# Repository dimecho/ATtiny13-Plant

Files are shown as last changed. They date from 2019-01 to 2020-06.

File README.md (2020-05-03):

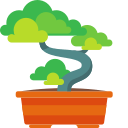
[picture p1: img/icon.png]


# ATtiny13 Plant

Monitor soil moisture and water plant. Portable and high efficiency with lithium-ion batteries.

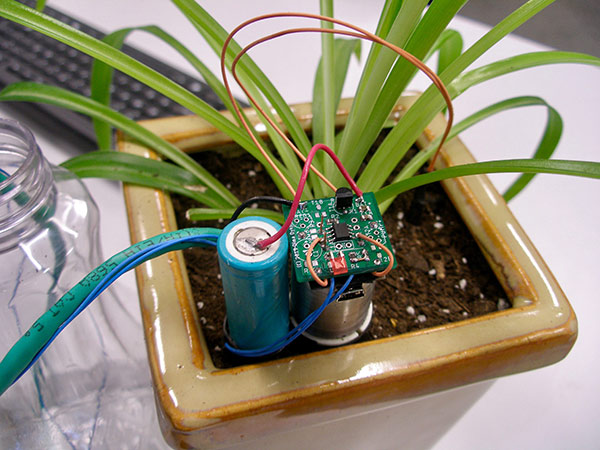
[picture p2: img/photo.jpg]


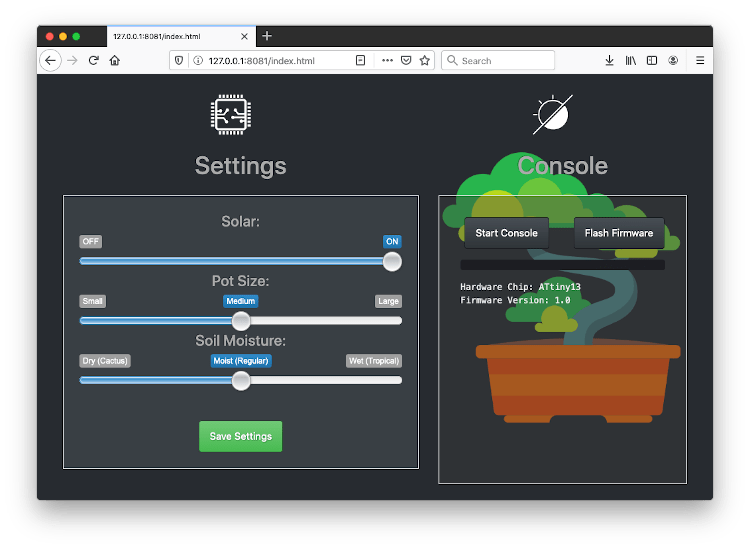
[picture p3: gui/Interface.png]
GUI


## Download

MacOS [MacOS](../../releases/download/1.0/ATtiny13-Plant.dmg)

Windows [Windows](../../releases/download/1.0/ATtiny13-Plant.zip)

Linux [Linux](../../releases/download/1.0/ATtiny13-Plant.tgz)

Firmware [Firmware](../../releases/download/1.0/ATtiny13-Plant-Firmware.zip)

## BOM (Bill of Materials)

| Part  | Value | Package | Function |
| ----- |:---:| ---:|---:|
| IC1 | ATTINY13A  | SOP-8 or DIP-8 | CPU |
| C1 | 100nF | 0805 or 0603 (104)  | CPU |
| T1A/B | 2N4401 NPN | TO-92 or SOT-23 | Pump |
| R1 | 100R | 0805 or 0603 (101)  | Pump |
| R2 | 10k | 0805 or 0603 (103)  | Pump |
| R6 | 10k | 0805 or 0603 (103)  | Sensor |
| LED1  | Red | 0805 or DIP-2 | LED |
| R7 | 1k | 0805 or 0603 (102)  | LED |
| - | 3.7-4.2V | Lithium 18650 | Battery  |
| - | TP4056 | Lithium Charger | Charger  |

## PCB

Designed with [EagleCAD](https://www.autodesk.com/products/eagle/free-download)

## Diagram

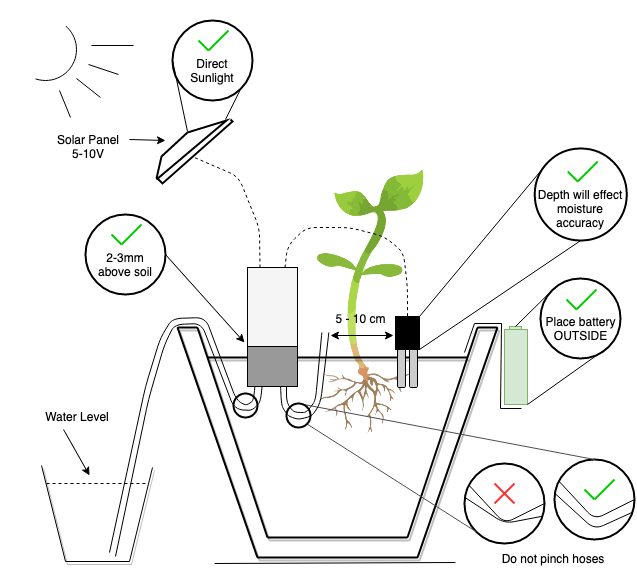
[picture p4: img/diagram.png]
Diagram


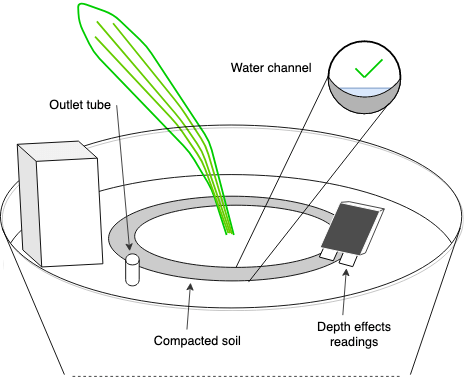
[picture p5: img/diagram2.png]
Operational


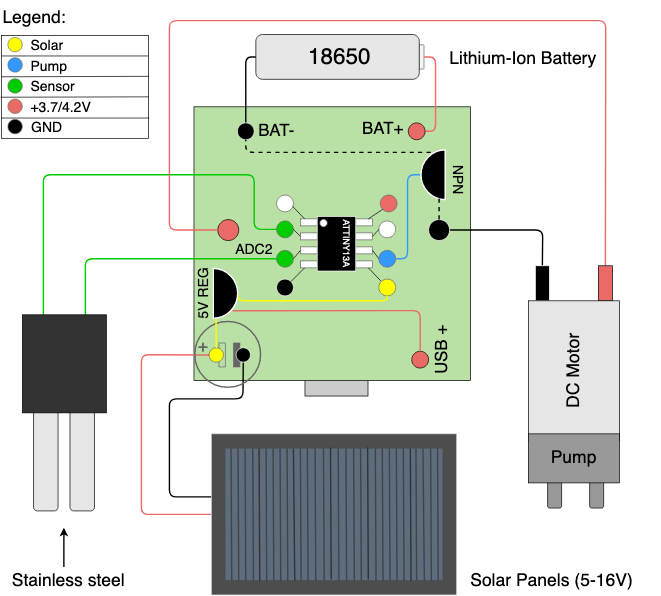
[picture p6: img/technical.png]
Technical


## Compile

Install "avr-gcc" and run "make".

> [MacOS](https://ww1.microchip.com/downloads/en/DeviceDoc/avr8-gnu-toolchain-osx-3.6.2.503-darwin.any.x86_64.tar.gz)
>
> [Windows](https://ww1.microchip.com/downloads/en/DeviceDoc/avr8-gnu-toolchain-3.6.2.1759-win32.any.x86.zip)

```
avr-gcc -std=gnu99 -Wall -Os -mmcu=attiny13a main.c -o main.o
avr-objcopy -O binary main.o main.bin
avr-objcopy -O ihex main.o main.hex
```

## Flash

```
avrdude -p t13 -c usbtiny -Uhfuse:w:0xFB:m -Ulfuse:w:0x6A:m -U flash:w:main.hex:i
```

There are 3 options to flash ATtiny13 chip.

1. [USBtiny](usbtiny) (built-in)
2. [USBasp](usbasp)
3. [Raspberry Pi](usbpi)

## Licenses

> ATtiny13 Plant
>
> 
>
> USBasp / USBtiny
>
> GNU (https://www.gnu.org/licenses/)

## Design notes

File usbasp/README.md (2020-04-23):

USBASP KEY
==========

http://fabiobaltieri.com/2011/09/02/usb-key-avr-programmer/

This project is an AVR ISP programmer with USB interface in a compact usb
key PCB. The project is based on the original USBasp version of Thomas Fischl,
which can be found on:

http://www.fischl.de/usbasp/

Contents
--------

    COPYING     text version of the GPL
    README      this file
    binaries/   pre-built firmware images in hex format
    firmware/   source directory for firmware files
    hardware/   source directory for the hardware design files

Firmware
--------

Building requires an avr-gcc toolchain, in the firmware/ directory, to build
run:

    make main.hex

Flashing the firmware on the device requires avrdude and a compatible hardware
programmer. Default configuration is stored at the beginning of the Makefile.
To program with the default configuration, run:

    make flash

Fuses can be configured running:

    make fuses

Hardware
--------

All hardware files (schematic, layout and libraries) are in CadSoft Eagle
format.

```
avrdude -p t13 -c usbasp -Uhfuse:w:0xFB:m -Ulfuse:w:0x6A:m -U flash:w:main.hex:i
```

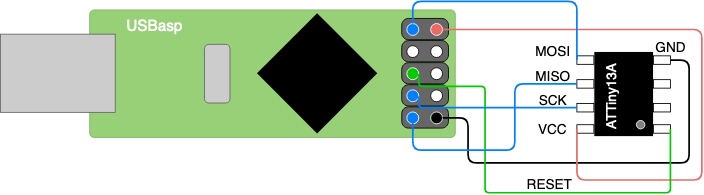
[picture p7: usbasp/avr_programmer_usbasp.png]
USBASP


License
-------

This program is free software: you can redistribute it and/or modify
it under the terms of the GNU General Public License as published by
the Free Software Foundation, either version 2 of the License, or
(at your option) any later version.

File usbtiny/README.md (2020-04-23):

http://www.simpleavr.com/avr/vusbtiny

Description
-------

From http://www.xs4all.nl/~dicks/avr/usbtiny/

USBtiny is a software implementation of the USB low-speed protocol for the Atmel ATtiny microcontrollers. Of course, it will also work on the ATmega series. The software is written for an AVR clocked at 12 MHz. At this frequency, each bit on the USB bus takes 8 clock cycles, and with a lot of trickery, it is possible to decode and encode the USB waveforms by software. The USB driver needs approximately 1250 to 1350 bytes of flash space (excluding the optional identification strings), depending on the configuration and compiler version, and 46 bytes RAM (excluding stack space). The C interface consists of 3 to 5 functions, depending on the configuration.

vUSB
-------

From http://www.obdev.at/products/vusb/

V-USB is a software-only implementation of a low-speed USB device for Atmel's AVR microcontrollers, making it possible to build USB hardware with almost any AVR microcontroller, not requiring any additional chip.

Features
-------

* Programming logic from usbtiny isp, mature avr-dude support
* Small foot-print
* Minimal components
* Powers target device

Note that the IO lines to the target MCUS are not protected. you can add 1k-2k resistors to SCK and MOSI and protect against possible wrong connections

References
-------

based on the works found at

v-usb from framework http://www.obdev.at/vusb/
usbtiny isp http://www.xs4all.nl/~dicks/avr/usbtiny/

Parts List
-------

* 1x attiny45/85
* 1x 100nf capacitor (104)
* 2x 3.6v zener diodes (1n747,BZX79)
* 2x 68ohm resistor
* 1x 1.5k (1.7k) resistor

* (optional) 1k/2k resistors for io lines protection

Tools Required
-------
* A working AVR programmer (yes, it's a catch22, we need one to make one)
* Working AVR programming environment

Application Notes
-------

* vusbtiny works with avrdude and is viewed by avrdude as a usbtiny programmer
* vusbtiny always power target chip via USB
* Jumper J2 connects programmer to target chip
* When connected and NOT in programming
* Target chip w/ target RESET line high
* Other target pins (MISO, MOSI, CLK) in hi-Z state
* During programming
* Turns target RESET line LOW
* MISO becomes input
* MOSI, CLK becomes output

Schematic
-------

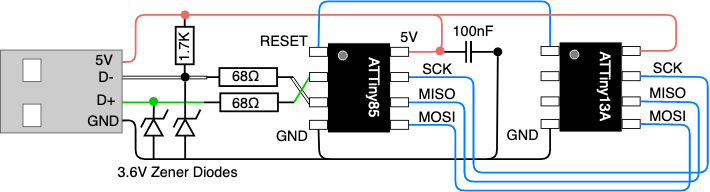
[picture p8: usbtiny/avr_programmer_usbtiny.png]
USBTINY


Building and Flashing
-------

* change into /firmware working directory
```
make
```
* attach your favorite ISP programmer
* modify makefile and change your avrdude parameters if needed. the stock one assumes USBTiny programmer. i.e. AVRDUDE_PROGRAMMERID=usbtiny
```
make install
```
After flashing firmware, we need to properly set the fuse, we are using pin 1 reset as IO in this project

* PLL clock used as required by v-usb layer for usb timing (16.5Mhz)
* reset pin disabled as we need to use it as IO
```
avrdude -c usbtiny -p t85 -V -U lfuse:w:0xe1:m -U hfuse:w:0x5d:m -U efuse:w:0xff:m
```

This setting disables further programming via 5V SPI as we need the RESET pin (pin1) for IO. you will need access to a HVSP programmer to recover the fuse.

Troubleshooting
-------

* Cannot flash the firmware? check your original programmer, might need to adjust timing via -B flag in avrdude. try to read chip 1st, may be a bad fuse, may be your chip need an external clock signal. you may need to fix your chip back to default 1st.
    check connections
* If use different io pins, check code and connections
* You may substitute zener diodes with 500mw, 400mw types
* You may try reduce R3 value to 1.2K or less
* You are more likely to encounter avrdude timing problems, try -B flag of avrdude, have a shorter USB cable all helps

License
-------

GPL2

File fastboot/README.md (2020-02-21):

### Bootloader

Bootloader is usefull for updating the firmware over UART without desoldering the chip. It also frees up RESET pin as IO (see Caution note).

Compile
```
cd ./bootloader
make
```
One-Time Flash
```
avrdude -p t13 -c linuxgpio -Uhfuse:w:0xEE:m -Ulfuse:w:0x6A:m -e -U flash:w:bootload.hex:i
```
Update (MacOS)
```
./fastboot/osx/bootloader -d /dev/cu.usbserial -b 9600 -p main.hex
```
Update (Windows)
```
./fastboot/win/FBOOT.EXE -C2 -B9600 -Pmain.hex
```

**Caution:** RESET Pin1 (PB5) if fuses set HFuse 0xFE (or 0xEE), bootloader can only be flashed once. Future flashing requires "High-Voltage programmer" to clear the fuse.

## License

GNU (https://www.gnu.org/licenses/)

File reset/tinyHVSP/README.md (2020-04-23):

http://www.simpleavr.com/avr/hvsp-fuse-resetter

Description
-------

Revert RESET fuse to factory default fuse settings.

Features
-------

* Reads device signature and hi-low fuses for hi-voltage serial programmable attinys
* Reset hi-low fuses to factory default on target devices
* Layout to drop-on attiny13, attiny25/45/85 8 pin devices targets
* Attiny24/44/84 targets needs additional breadboard and jumper wires
* Standalone operations, fuses values show on 7 segment display
* Cannot reset fuse for attiny2313 and atmega devices as they requires hi-voltage parallel programming

Parts List
-------

* attiny2313
* 4x7 segment LED display
* 1k resistor x 2
* 2n2222 NPN transistor or equivalent
* 78L05
* +12V battery source

Schematic
-------

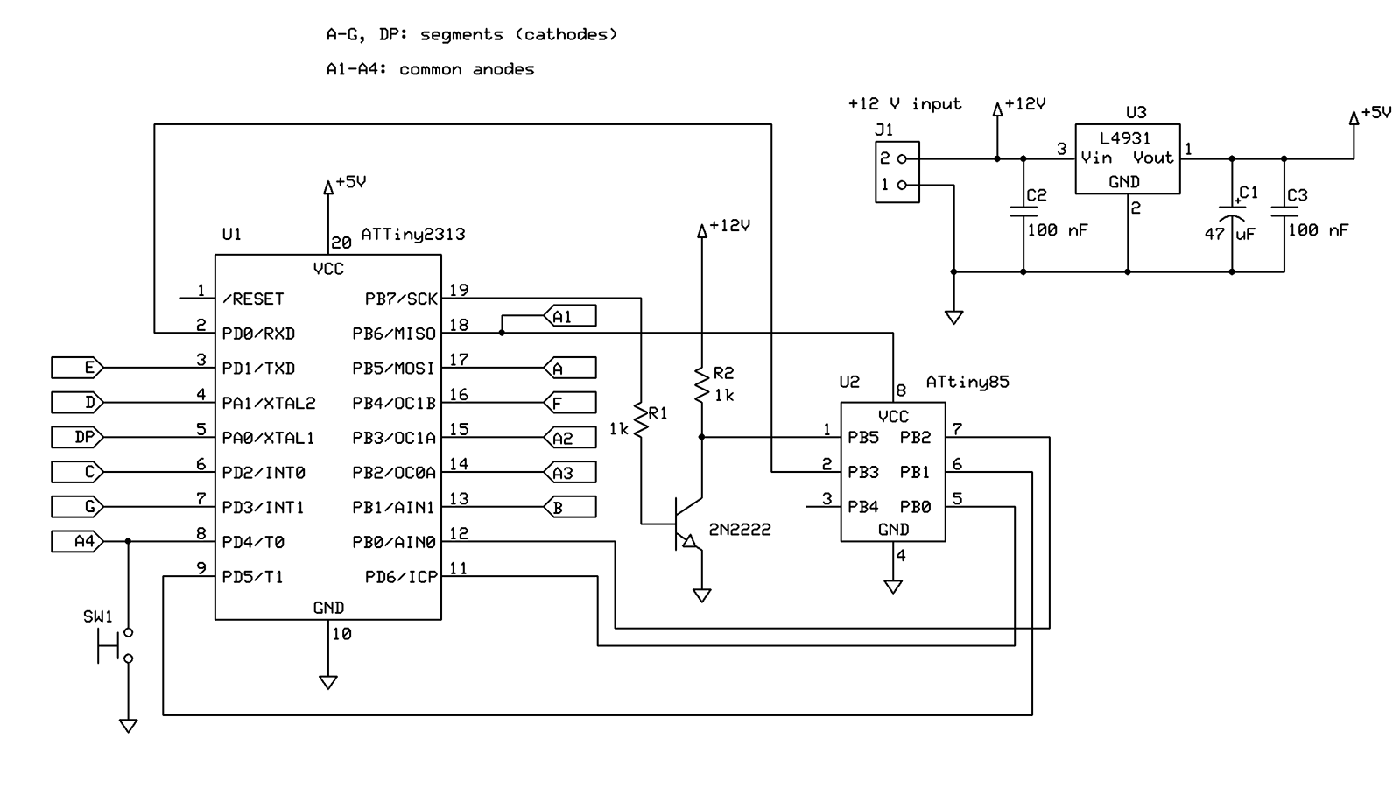
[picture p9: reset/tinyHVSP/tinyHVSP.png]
Schematic


Project FUSE Setting
-------

```
avrdude -c usbtiny -p t2313 -V -U lfuse:w:0xe4:m -U hfuse:w:0xdf:m -U efuse:w:0xff:m
```

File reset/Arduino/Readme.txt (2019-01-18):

Wire-up ATTiny chip into Arduino that needs its fuses fixed (see schematics for details) and load ATTinyFuseReset.ino sketch. In the Arduino IDE open Serial Monitor and select 19200 baud as the serial rate. Then send a character to the Arduino using the Serial Monitor's "send" button to trigger the fuse reset cycle. The code will print out the device signature and before and after values of the fuses.

You should now have a functional ATTiny!

Source: https://sites.google.com/site/wayneholder/attiny-fuse-reset

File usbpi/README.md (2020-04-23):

## Flash ATtiny13 with Raspberry Pi (linuxgpio)
```
avrdude -p t13 -c linuxgpio -Uhfuse:w:0xFB:m -Ulfuse:w:0x6A:m -U flash:w:main.hex:i
```

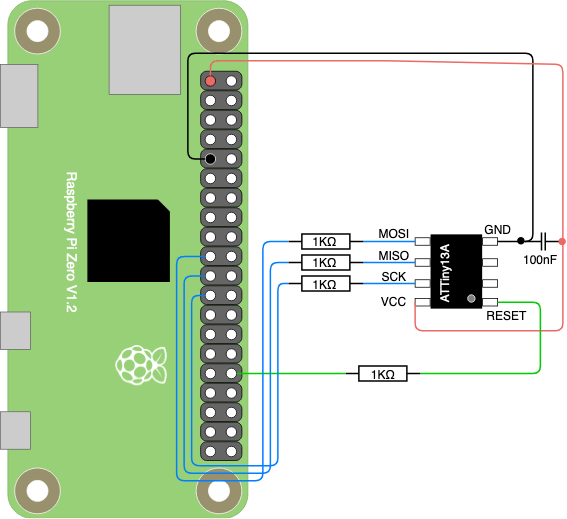
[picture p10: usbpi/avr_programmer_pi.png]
PI


Install AVRDude.
```
sudo apt-get install avrdude
```
Open AVRDude configuration file for editing.
```
sudo nano /etc/avrdude.conf
```
In Nano, use ctrl-w to search for linuxgpio. This is the section that controls the GPIO pins used for programming. The section needs to be uncommented. Set the MOSI, MISO and SCK entries to the GPIO pins on the Pi.
```
programmer
  id    = "linuxgpio";
  desc  = "Use the Linux sysfs interface to bitbang GPIO lines";
  type  = "linuxgpio";
  reset = 12;
  sck   = 11;
  mosi  = 10;
  miso  = 9;
```

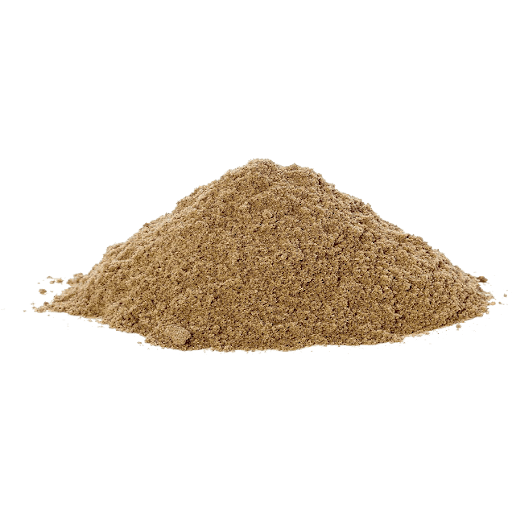
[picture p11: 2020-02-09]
gui/Web/img/sand.png

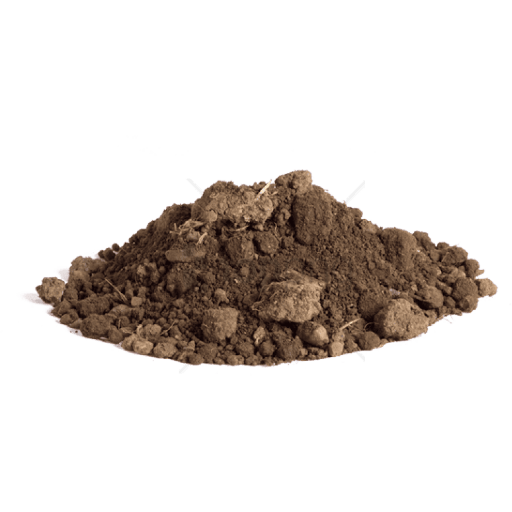
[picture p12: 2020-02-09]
gui/Web/img/dirt.png

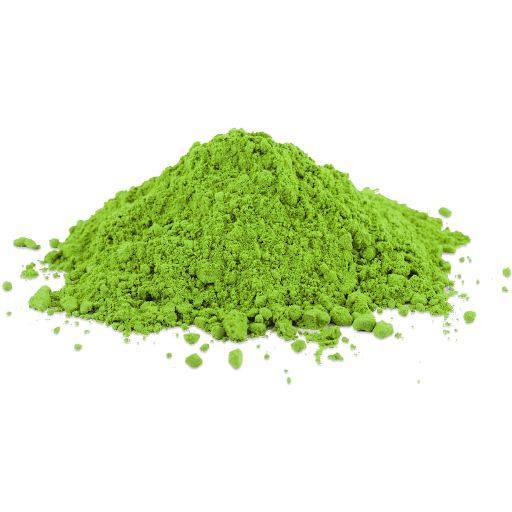
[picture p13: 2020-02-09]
gui/Web/img/moss.png

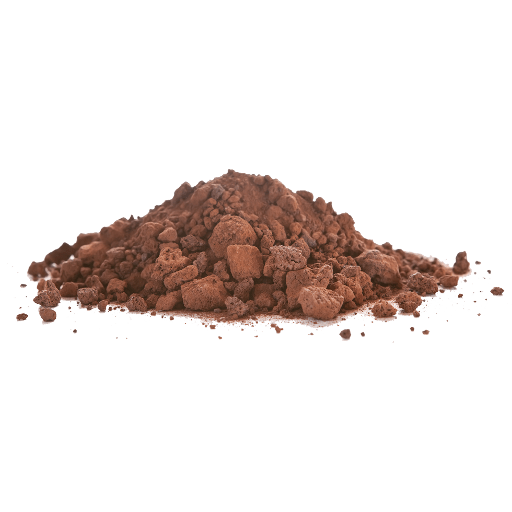
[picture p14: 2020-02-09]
gui/Web/img/clay.png

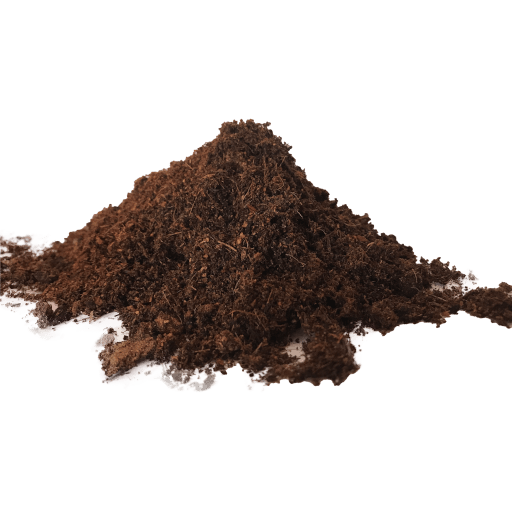
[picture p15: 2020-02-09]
gui/Web/img/loam.png

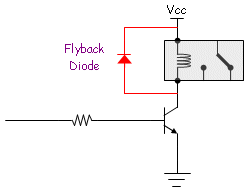
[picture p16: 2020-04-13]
img/flyback_diode.png

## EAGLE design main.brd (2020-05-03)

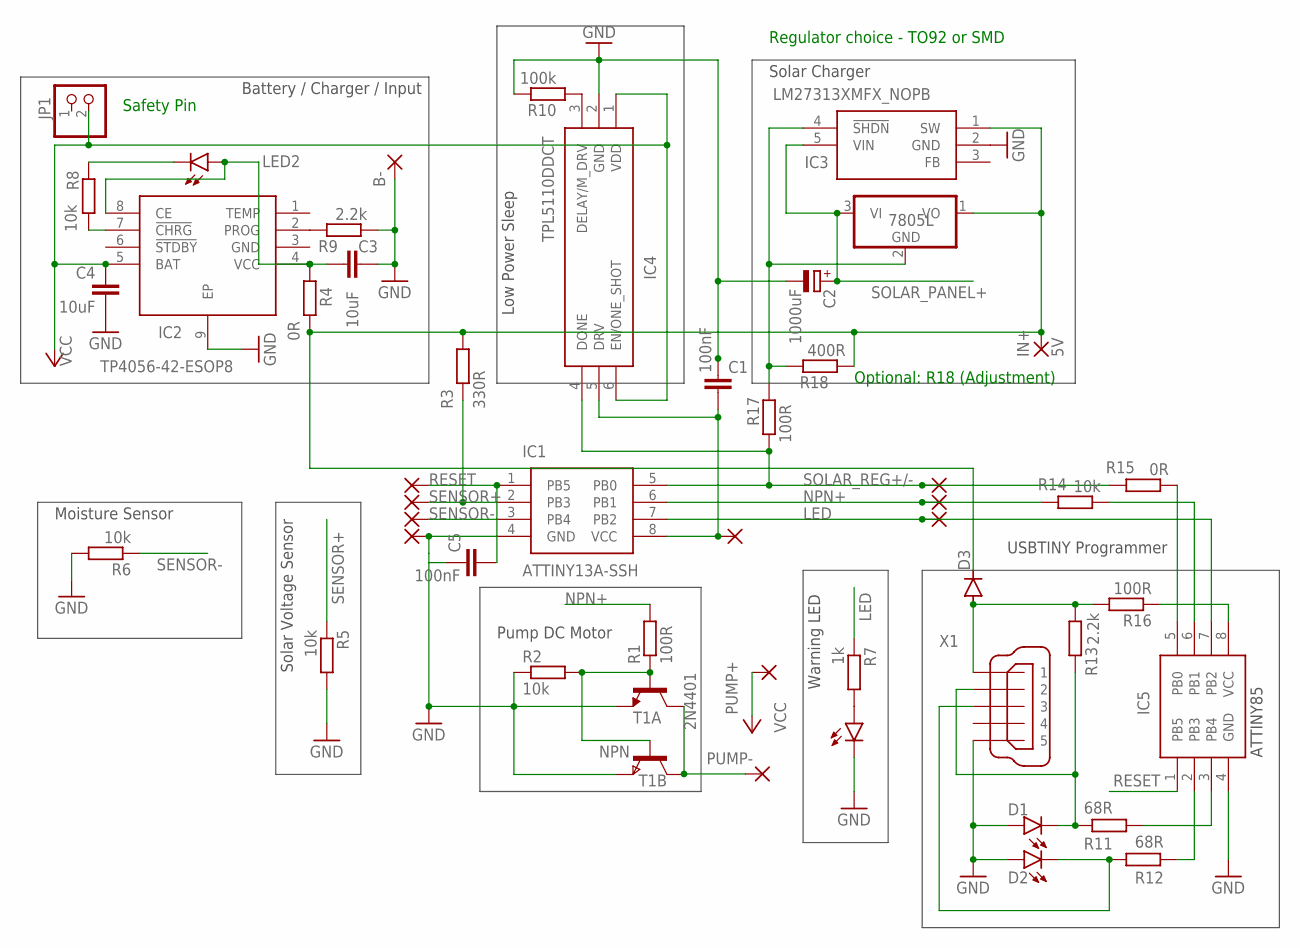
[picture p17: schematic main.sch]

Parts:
B-: 1,6/0,8
C1, C5: 100nF; C0805
C2: 1000uF; E2,5-7
C3: 10uF; C3216
C4: 10uF; C0805
D1, D2: LEDSML0805; SML0805
D3: DIODE-MINIMELF; MINIMELF
IC1, IC5: ATTINY13A-SSH; SOIC127P600X175-8N
IC2: TP4056-42-ESOP8; SOIC127P600X175-9N
IC3: LM27313XMFX_NOPB; SOT95P280X145-5N
IC4: TPL5110DDCT; SOT95P280X110-6N
IN+: 5V; 1,6/0,9
JP1: PINHD-1X2; 1X02
LED1, LED2: LEDSML0805; SML0805
PAD3, PAD4, PAD5, PAD6, PAD7, PAD8, PAD9, PAD10: 1,6/0,8
PUMP+: 2,15/1,0
PUMP-: 2,15/1,0
R1: 100R; R0805
R2, R5, R6: 10k; R0805
R3: 330R; R0805
R4: 0R; M1206
R7: 1k; R0805
R8: 10k; R0603
R9, R13: 2.2k; R0603
R10: 100k; R0603
R11, R12: 68R; R0603
R14: 10k; R0402
R15: 0R; R0402
R16, R17: 100R; R0603
R18: 400R; R0603
REG1: 7805L; TO92
T1A: 2N4401; TO92
T1B: NPN; SOT-23
X1: MINI-USB-UX60A-MB-5ST; UX60A-MB-5ST

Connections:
GND: B-.1, C1.1, C2.-, C3.2, C4.2, C5.1, D1.A, D2.A, IC1.4 (GND), IC2.9 (EP), IC3.2 (GND), IC4.2 (GND), IC5.4 (GND), LED1.C, PAD7.1, R2.1, R5.2, R6.2, R9.2, R10.2, T1A.1 (E), T1B.2 (E), X1.5
LED: IC1.7 (PB2), IC5.7 (PB2), PAD4.1, R7.1
unnamed: R1.1, R2.2, T1A.2 (B), T1B.3 (B)
unnamed: PUMP-.1, T1A.3 (C), T1B.1 (C)
unnamed: C1.2, IC1.8 (VCC), IC4.5 (DRV), PAD3.1
unnamed: C3.1, IC2.4 (VCC), IC2.8 (CE), LED2.A, R4.2
unnamed: D3.C, IC3.1 (SW), IN+.1, R3.2, R4.1, R18.1, REG1.1 (VO)
unnamed: LED1.A, R7.2
unnamed: IC4.3 (DELAY/M_DRV), R10.1
unnamed: IC2.7 (!CHRG), R8.2
unnamed: LED2.C, R8.1
unnamed: IC5.3 (PB4), R11.2
unnamed: IC2.2 (PROG), R9.1
unnamed: IC5.2 (PB3), R12.2
unnamed: D1.C, R11.1, R13.2, X1.2
unnamed: D2.C, R12.1, X1.3
unnamed: IC5.6 (PB1), R14.1
unnamed: IC5.5 (PB0), R15.1
unnamed: IC5.8 (VCC), R16.1
unnamed: IC3.4 (!SHDN), R17.2, R18.2, REG1.2 (GND)
unnamed: D3.A, R13.1, R16.2, X1.1
NPN+: IC1.6 (PB1), PAD6.1, R1.2, R14.2
RESET: C5.2, IC1.1 (PB5), IC5.1 (PB5), PAD10.1
SENSOR+: IC1.2 (PB3), PAD9.1, R3.1, R5.1
SENSOR-: IC1.3 (PB4), PAD8.1, R6.1
SOLAR_PANEL+: C2.+, IC3.5 (VIN), REG1.3 (VI)
SOLAR_REG+/-: IC1.5 (PB0), IC4.4 (DONE), PAD5.1, R15.2, R17.1
VCC: C4.1, IC2.5 (BAT), IC4.1 (VDD), IC4.6 (EN/ONE_SHOT), JP1.2, PUMP+.1

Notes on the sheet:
Battery / Charger / Input
Solar Charger
Pump DC Motor
Warning LED
Moisture Sensor
Solar Voltage Sensor
Low Power Sleep
ATTINY85
USBTINY Programmer
Safety Pin
Regulator choice - TO92 or SMD
Optional: R18 (Adjustment)

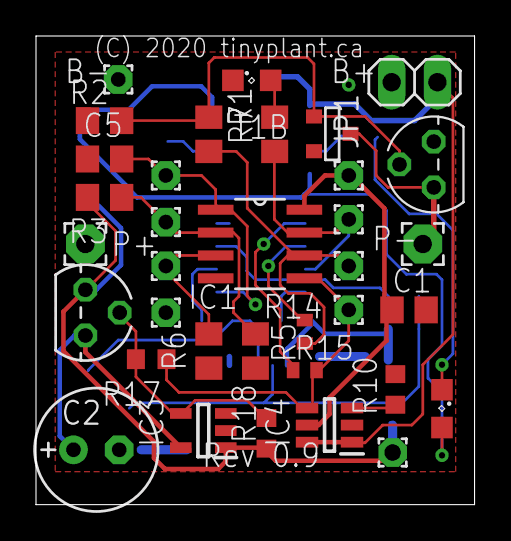
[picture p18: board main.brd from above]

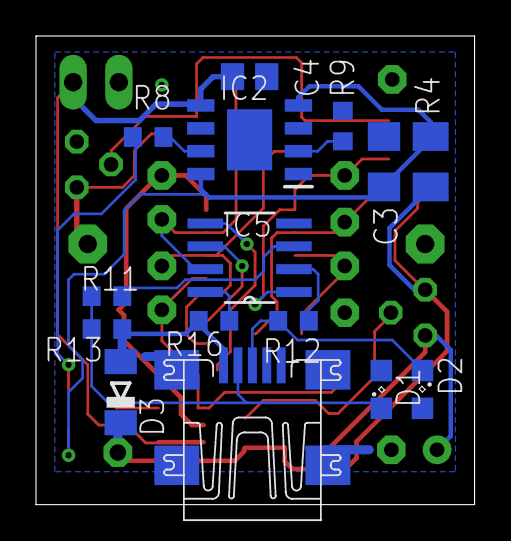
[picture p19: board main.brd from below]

Board: 2 copper layers, 24.4 x 26.0 mm, 50 parts (15 on the bottom side), 28 nets.

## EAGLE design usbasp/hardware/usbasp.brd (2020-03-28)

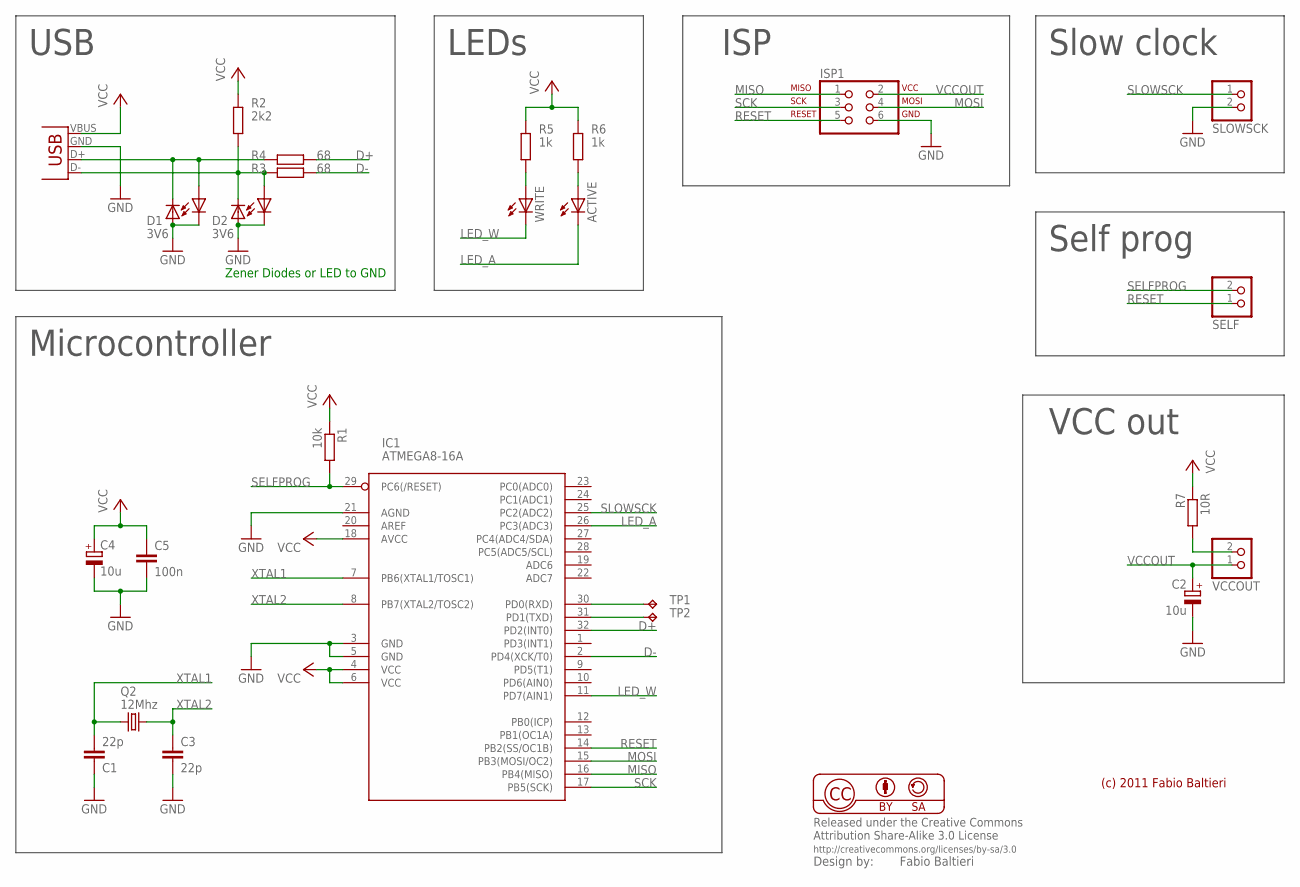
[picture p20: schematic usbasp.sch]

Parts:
ACTIVE: LEDCHIP-LED0805; CHIP-LED0805
C1, C3: 22p; C0805
C2, C4: 10u; SMC_A
C5: 100n; C0805
D1, D2: 3V6; SMA-DIODE
IC1: ATMEGA8-16A; TQFP32-08
ISP1: ISP-AVR910SMD; 2X03_BORDER
LED1, LED2: LEDCHIP-LED0805; CHIP-LED0805
Q2: 12Mhz; HC49US
R1: 10k; M0805
R2: 2k2; M0805
R3, R4: 68; M0805
R5, R6: 1k; M0805
R7: 10R; M0805
SELF: PINHD-1X2; 1X02
SLOWSCK: PINHD-1X2; 1X02
TP1, TP2: TPB1,27; B1,27
VCCOUT: PINHD-1X2; 1X02
WRITE: LEDCHIP-LED0805; CHIP-LED0805
X1: USB-A-H

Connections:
D+: IC1.32 (PD2(INT0)), R4.1
D-: IC1.2 (PD4(XCK/T0)), R3.1
GND: C1.1, C2.-, C3.1, C4.-, C5.2, D1.A, D2.A, IC1.3 (GND), IC1.5 (GND), IC1.21 (AGND), ISP1.6, LED1.C, LED2.C, SLOWSCK.2, X1.GND (VBUS)
LED_A: ACTIVE.C, IC1.26 (PC3(ADC3))
LED_W: IC1.11 (PD7(AIN1)), WRITE.C
MISO: IC1.16 (PB4(MISO)), ISP1.1
MOSI: IC1.15 (PB3(MOSI/OC2)), ISP1.4
unnamed: R5.2, WRITE.A
unnamed: D1.C, LED1.A, R4.2, X1.D+ (D-)
unnamed: D2.C, LED2.A, R2.1, R3.2, X1.D- (D+)
unnamed: ACTIVE.A, R6.2
unnamed: IC1.30 (PD0(RXD)), TP1.TP
unnamed: R7.2, VCCOUT.2
unnamed: IC1.31 (PD1(TXD)), TP2.TP
RESET: IC1.14 (PB2(SS/OC1B)), ISP1.5, SELF.1
SCK: IC1.17 (PB5(SCK)), ISP1.3
SELFPROG: IC1.29 (PC6(/RESET)), R1.2, SELF.2
SLOWSCK: IC1.25 (PC2(ADC2)), SLOWSCK.1
VCC: C4.+, C5.1, IC1.4 (VCC), IC1.6 (VCC), IC1.18 (AVCC), R1.1, R2.2, R5.1, R6.1, R7.1, X1.VBUS (GND)
VCCOUT: C2.+, ISP1.2, VCCOUT.1
XTAL1: C1.2, IC1.7 (PB6(XTAL1/TOSC1)), Q2.2
XTAL2: C3.2, IC1.8 (PB7(XTAL2/TOSC2)), Q2.1

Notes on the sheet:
(c) 2011 Fabio Baltieri
Microcontroller
USB
LEDs
ISP
Slow clock
Self prog
VCC out
Zener Diodes or LED to GND

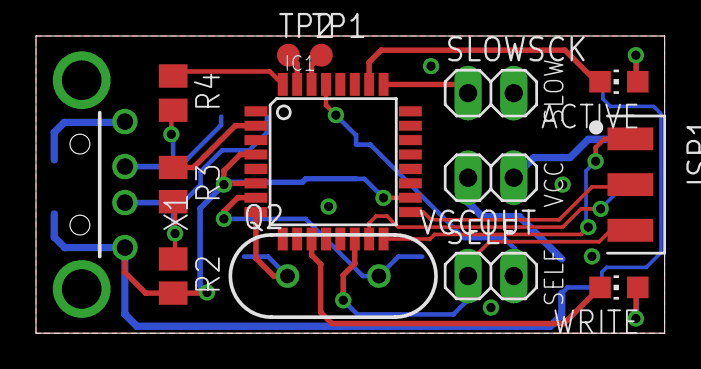
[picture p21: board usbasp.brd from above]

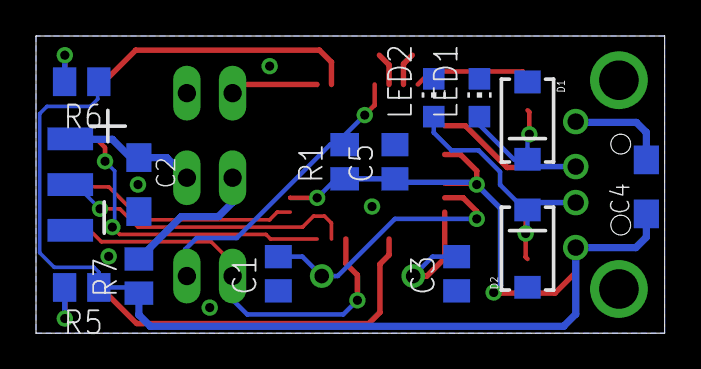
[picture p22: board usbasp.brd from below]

Board: 2 copper layers, 34.9 x 16.5 mm, 27 parts (13 on the bottom side), 22 nets.

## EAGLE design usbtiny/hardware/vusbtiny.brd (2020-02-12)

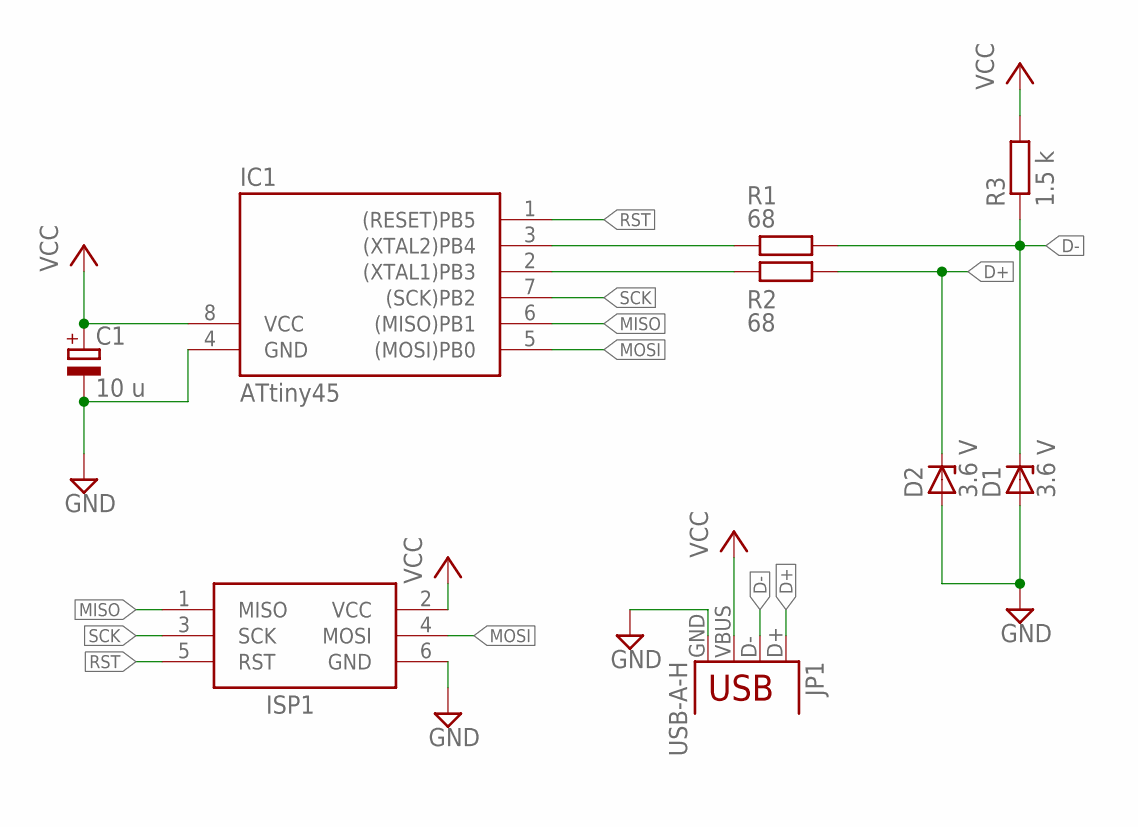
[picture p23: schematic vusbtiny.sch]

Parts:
C1: 10 u; E2,5-5
D1, D2: 3.6 V; DO34Z7
IC1: ATtiny45; DIL08
ISP1: AVRISP-6; AVRISP
JP1: USB-A-H
R1, R2: 68; 0207/10
R3: 1.5 k; 0207/10

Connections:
D+: D2.C, JP1.D+, R2.2
D-: D1.C, JP1.D-, R1.2, R3.1
GND: C1.-, D1.A, D2.A, IC1.4 (GND), ISP1.6 (GND), JP1.GND
MISO: IC1.6 ((MISO)PB1), ISP1.1 (MISO)
MOSI: IC1.5 ((MOSI)PB0), ISP1.4 (MOSI)
unnamed: IC1.3 ((XTAL2)PB4), R1.1
unnamed: IC1.2 ((XTAL1)PB3), R2.1
RST: IC1.1 ((RESET)PB5), ISP1.5 (RST)
SCK: IC1.7 ((SCK)PB2), ISP1.3 (SCK)
VCC: C1.+, IC1.8 (VCC), ISP1.2 (VCC), JP1.VBUS, R3.2

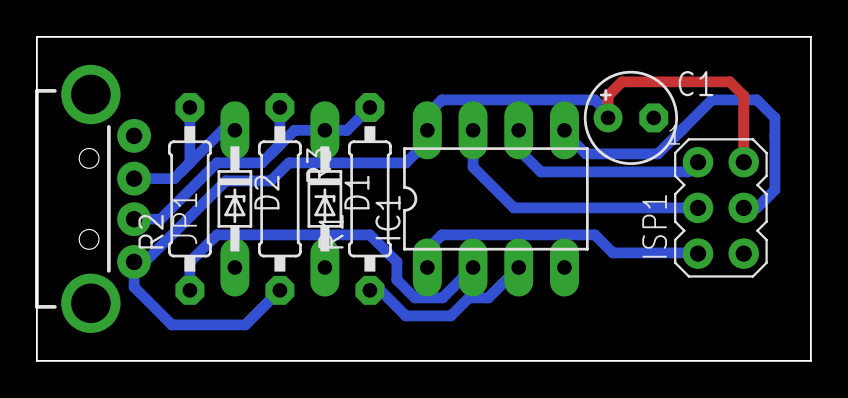
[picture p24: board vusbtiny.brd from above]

Board: 2 copper layers, 43.0 x 18.0 mm, 9 parts (0 on the bottom side), 10 nets.

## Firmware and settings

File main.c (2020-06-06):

/*  
    FUSE_L=0x6A (Clock divide fuse enabled = 8Mhz CPU frequency is actually 1MHz)
    FUSE_H=0xFF (0xFF (no bootloader) / 0xEE (bootloader) = RSTDISBL + SELFPRGEN -> CATION: If enabled chip can only be programmed once)
    FUSE_H=0xFB (BODLEVEL 0xFD = 1.8V, 0xFB = 2.7V, 0xFF = BOD Disabled)

    ** The brown-out detector is designed to put the chip into reset when the voltage gets too low,
        and hold it in reset until the voltage returns back to a safe operating level.
*/
#ifndef F_CPU
    #if defined __AVR_ATtiny45__ || defined __AVR_ATtiny85__
        #define F_CPU 1000000 //CPU @ 8Mhz / 8 = 1 Mhz
    #else
        #define F_CPU 1200000 //CPU @ 9.6Mhz / 8 = 1.2Mhz
        //#define F_CPU 128000 //CPU @ 128Khz (no clock divide)

        //WARNING: @128Khz do not divide clock by 8 (LFUSE:6B) - ATtiny 13 will be bricked
        //Recovery: See "arduino_isp_boot-selectable_serial-config_slow_spi.cpp"
    #endif
#endif
/*
                             [ATtiny13A]
                              +------+
                [RESET] PB5  1| O    |8  VCC (2.7V - 4.8V)
(Sensor OUT / Solar IN) PB3  2|      |7  PB2 [CLK]  (LED)
(Sensor IN)             PB4  3|      |6  PB1 [MISO] (Pump)
                        GND  4|      |5  PB0 [MOSI] (Solar ON (WS78L05) / Sleep (TPL5110))
                              +------+
*/
#ifndef SERIAL
    #define SERIAL 0 //Serial # (identify multiple devices)
#endif
/* HARDWARE CONFIGURATION */
/*------------------------*/
#define WS78L05 1 //WS78L05 = cheap
//#define LM2731 2 //LM2731 = expensive
//#define TPL5110 3 //TPL5110 = most expensive
#define EEPROM_ENABLED
//#define UART_TX_ENABLED
//#define UART_RX_ENABLED
#define SOLAR_ENABLED
#define SENSORLESS_ENABLED
/*------------------------*/

//#include <avr/pgmspace.h>
//#include <stdio.h>
//#include <string.h>
#include <avr/io.h>
#include <util/delay.h>
#include <avr/interrupt.h>
#include <avr/sleep.h>
#include <avr/wdt.h>
#include <avr/power.h>

/*
www.mtcnet.net/~henryvm/wdt/wd.h
The watchdog has a timeout period. If you do not set a flag before a timeout period has elapsed then the watchdog
will reset the uC and your program will start at the beginning. An automatic "reboot"
*/
#define soft_reset()        \
do                          \
{                           \
    cli();				 	\
    WDTCR |= (0<<WDP3) | (0<<WDP2) | (0<<WDP1) | (0<<WDP0); \
    while(1);               \
}while(0)
/*
CAUTION!
Older AVRs will have the watchdog timer disabled on a reset.
Newer AVRs once the watchdog is enabled, it stays enabled even after a reset!
For these newer AVRs a function needs to be added to the .init3 section (i.e. during the startup code, before main())
to disable the watchdog early enough so it does not continually reset the AVR.
*/
/*
void wdt_init(void) __attribute__((naked)) __attribute__((section(".init3")));
void wdt_init(void) {
	/
    In safety level 1, WDE is overridden by WDRF in MCUSR. See “MCUSR – MCU Status Regis-ter” on page 46 for description of WDRF.
    This means that WDE is always set when WDRF is set. To clear WDE, WDRF must be cleared before disabling the Watchdog.
    This feature ensures multiple resets during conditions causing failure, and a safe start-up after the failure.
	/
    MCUSR = 0;
    wdt_disable();
    return;
}
*/

#ifndef versionID
    #define versionID               10 //1.0
#endif
#ifndef sensorMoisture
    #define sensorMoisture          660 //ADC value
#endif
#ifndef potSize
 #define potSizeTimer               20 //20x2x100 = 4000 miliseconds (minus 1 seconds prime) = 3 seconds pump
#endif

#define pumpPin                     PB1 //Output
#define sensorPin                   PB3 //Output
#define solarPin                    PB0 //Output
#define ledPin                      PB2 //Output
#define solarSensorPin              PB3 //Input/Output
#define moistureSensorPin           PB4 //Input
#define delayWatering               50  //8 seconds x 50 = 6.5 min
#define delayBetweenRefillReset     20  //8 seconds x 40 x 20 = 2 hours
#define delayBetweenOverfloodReset  100 //8 seconds x 40 x 100 = 8 hours
#define delayBetweenSolarDischarge  4   //8 seconds x 5 = .5 min

#ifdef EEPROM_ENABLED
    //#include <avr/eeprom.h>
    static uint8_t EEPROM_read(uint8_t ucAddress);
    static void EEPROM_write(uint8_t ucAddress, uint8_t ucValue);
    static void EEPROM_save(uint8_t ucAddress, uint16_t ucValue, uint8_t ee);
#endif

#define UART_BAUDRATE   (9600)

#ifdef UART_TX_ENABLED
    #define TXDELAY         (uint8_t)(((F_CPU/UART_BAUDRATE)-7 +1.5)/3)
    #define UART_TX         PB3 // Use PB3 as TX pin
    void uart_putc(char c);
    void uart_putu(uint16_t x);
    void uart_puts(const char *s);
#endif

#ifdef UART_RX_ENABLED
    #define RXDELAY          (int)(((F_CPU/UART_BAUDRATE)-5 +1.5)/3)
    #define RXDELAY2         (int)((RXDELAY*1.5)-2.5)
    #define UART_RX          PB4 // Use PB4 as RX pin
    /*
    #define RXROUNDED         (((F_CPU/UART_BAUDRATE)-5 +2)/3)
    #if RXROUNDED > 127
    #error Low baud rates are not supported - use higher, UART_BAUDRATE
    #endif
    */
#endif

static void blink(uint8_t time, uint8_t duration);
static uint16_t sensorRead(uint8_t enablePin,uint8_t readPin);
static uint16_t ReadADC(uint8_t pin, uint8_t vref);

static uint16_t div3(uint16_t n);
//static uint16_t div10(uint16_t n);
/*
Tips and Tricks to Optimize Your C Code for 8-bit AVR Microcontrollers
https://ww1.microchip.com/downloads/en/AppNotes/doc8453.pdf
*/

#ifdef EEPROM_ENABLED
    uint8_t EEPROM_read(uint8_t ucAddress)
    {
        // Wait for completion of previous write
        while(EECR & (1<<EEPE))
        ;
        // Set up address register
        EEARL = ucAddress;
        // Start eeprom read by writing EERE
        EECR |= (1<<EERE);
        // Return data from data register
        return EEDR;
    }

    void EEPROM_write(uint8_t ucAddress, uint8_t ucValue)
    {
        // Wait for completion of previous write
        while(EECR & (1<<EEPE))
        ;
        // Set Programming mode
        //EECR = (0<<EEPM1)|(0>>EEPM0);
        EECR = (0<<EEPM1)|(0<<EEPM0);
        // Set up address and data registers
        EEARL = ucAddress;
        EEDR = ucValue;
        // Write logical one to EEMPE
        EECR |= (1<<EEMPE);
        // Start eeprom write by setting EEPE
        EECR |= (1<<EEPE);
    }

    void EEPROM_save(uint8_t ucAddress, uint16_t ucValue, uint8_t ee)
    {
    	//if (ee < 0xFF)
        if (ee == 0xEE || ee == 0xEF) //EEPROM wear reduction
        {
            if(ucValue > 255) //split into two epprom fields -> 388 = 38 + 8
            {
                uint8_t lo_hi[] = { (uint8_t)ucValue, (uint8_t)(ucValue >> 8) }; //0xAAFF = { 0xFF, 0xAA }
                EEPROM_write(ucAddress, lo_hi[0]);
                EEPROM_write((ucAddress + 1), lo_hi[1]);
            }else{
                EEPROM_write(ucAddress, ucValue);
                EEPROM_write((ucAddress + 1), 0); //255);
                //eeprom_write_word((uint16_t*)ucAddress, ucValue);
            }
        }
    }
#endif

//Wake Up CPU From Sleep Mode
ISR(WDT_vect) {
}
//ADC interrupt (must be in the code for the interrupt to work correctly)
ISR(ADC_vect) {
}

int main(void)
{
    //clock_prescale_set(3); //clock_div_8 = 3

    //=============
    //VARIABLE
    //=============
    uint16_t suitableMoisture = sensorMoisture; //Analog value with 10k pull-up resistor
    uint16_t deepSleep = delayWatering;
    uint8_t potSize = potSizeTimer;
    uint8_t runSolar = 0;
    uint8_t ee = 0xFF;
    uint16_t errorCode = 0;

    //=============
    //WATCHDOG
    //=============
    #if defined __AVR_ATtiny45__ || defined __AVR_ATtiny85__
    	WDTCR = (1<<WDIE);  // Enable watchdog timer interrupts
    #else
        WDTCR = (1<<WDTIE);  // Enable watchdog timer interrupts 
    #endif

    //=================================
    //AVR I/O pins are input by default
    //=================================
    /*
    DDRB |= (1<<pumpPin); //Digital OUTPUT
    DDRB |= (1<<solarPin); //Digital OUTPUT
    DDRB |= (1<<sensorPin); //Digital OUTPUT
    DDRB |= (1<<ledPin); //Digital OUTPUT
    */

    //Page 57 ATtiny13 Manual
    //MCUCR = 0x40;	//All Pins Pull-up disabled
    DDRB = 0xFF;	//All Pins (0-0-DDB5-DDB4-DDB3-DDB2-DDB1-DDB0)	OUTPUT = 1 | INPUT = 0
    PORTB = 0x00;   //All Pins (0-0-PB5-PB4-PB3-PB2-PB1-PB0)        ON = 1 | OFF = 0
    blink(10,4);	//Alive blink

    //=============
    //EEPROM
    //=============
    //eeprom_busy_wait();
    #ifdef EEPROM_ENABLED
        ee = EEPROM_read(0x02);
        //uint8_t ee = eeprom_read_byte((uint8_t*)0x02);
        if (ee == 0xFF) //EEPROM is blank
        {
            EEPROM_save(0x00,versionID,0xEE);
            EEPROM_save(0x02,sensorMoisture,0xEE);
            EEPROM_save(0x04,potSize,0xEE);
            EEPROM_save(0x06,runSolar,0xEE);
            EEPROM_save(0x08,deepSleep,0xEE);
            //EEPROM_save(0xA,0xFF,0xEE);

            #ifdef WS78L05
            	EEPROM_save(0xC,WS78L05,0xEE);
            #endif
            #ifdef LM2731
            	EEPROM_save(0xC,LM2731,0xEE);
            #endif
            #ifdef TPL5110
				EEPROM_save(0xC,TPL5110,0xEE);
            #endif

			EEPROM_save(0xE,SERIAL,0xEE); //Serial # - not UART

        }else{
            suitableMoisture = ee | (EEPROM_read(0x03) << 8);
            //suitableMoisture = eeprom_read_word((uint16_t*)0x02);

            potSize = EEPROM_read(0x04);
            //potSize = eeprom_read_byte((uint8_t*)0x04);

            runSolar = EEPROM_read(0x06);
            //runSolar = eeprom_read_byte((uint8_t*)0x06);
        }
        
        deepSleep = EEPROM_read(0x08) | (EEPROM_read(0x09) << 8);
        //deepSleep = eeprom_read_byte((uint8_t*)0x08);

        ee = EEPROM_read(0xA);
        //ee = eeprom_read_byte((uint8_t*)0xA);
        //EEPROM_save(0x01,0xFF,0xEE); //reset for next time
    #endif

    /*
    Note: Global variables cost a lot of flash size only use if needed.
    https://ww1.microchip.com/downloads/en/AppNotes/doc8453.pdf
    */
    uint16_t sleepLoop = 0;  //Track the passage of time
    uint8_t emptyBottle = 0;

    #ifdef UART_TX_ENABLED
        //================
        //ALIVE TEST
        //================
        //BODCR |= (1<<BODS)|(1<<BODSE); //Disable Brown Out Detector Control Register
        /*
        PORTB |= (1<<PB0); //ON
        _delay_ms(900);
        PORTB &= ~(1<<PB0); //OFF
        */
        uart_putc('.');
        uart_putu(versionID);
        //uart_putc('\r');
        //uart_putc('\n');
    #endif
    //================

    #ifdef SENSORLESS_ENABLED
        uint16_t moistureLog = 0;
    #endif

    /* 
    !!! IMPORTANT NOTE !!!

    "EEPROM Debug" avrdude will reset ATtiny on read loosing all variables.
    This means that variables like emptyBottle or moistureLog are difficult to debug.

    Solution: Write/Read to EEPROM while debugging.
    */

    if(runSolar == 1 || ee == 0xEE) {

    	emptyBottle = EEPROM_read(0x38);
        moistureLog = EEPROM_read(0x3A);

        //deepSleep = 0;
        //set_sleep_mode(SLEEP_MODE_IDLE);
        WDTCR |= (0<<WDP3) | (1<<WDP2) | (1<<WDP1) | (1<<WDP0); //Set timer 2s

    }else{
        //set_sleep_mode(SLEEP_MODE_PWR_DOWN);
        //Table 8-2 page 43
        WDTCR |= (1<<WDP3) | (0<<WDP2) | (0<<WDP1) | (1<<WDP0); //Set timer 8s (max)
        //----------------
        //wdt_enable(WDTO_8S); // 8s
        // Valid delays:
        //  WDTO_15MS
        //  WDTO_30MS
        //  WDTO_60MS
        //  WDTO_120MS
        //  WDTO_250MS
        //  WDTO_500MS
        //  WDTO_1S
        //  WDTO_2S
        //  WDTO_4S
        //  WDTO_8S
    }

    sei(); // enable all interrupts or we never wake

    for (;;) {

        //===========================
        //Preventative Measure - Always Shut OFF!
        //In rare cases if code skips (watchdog jump) and pump does not turn off, we force shut-off each sleep cycle
        //===========================
        PORTB &= ~(1<<pumpPin); //OFF
        
       	/*
        uint8_t resetAVR = ReadADC(ledPin);
        if(resetAVR > 250) {
            //EEPROM_save(0x2A,resetAVR,ee); //DEBUG
            //https://forum.arduino.cc/index.php?topic=149235.0
            /
            asm ("cli");                    // interrupts off
            asm volatile ("eor r1,r1");     // make sure zero-register is zero
            asm volatile ("ldi r16,0xFF");  // end of RAM (0xFF)
            asm volatile ("sts 0x5E,r16");  // SPH
            asm volatile ("sts 0x5D,r16");  // SPL
            asm volatile ("eor r31,r31");   // Clear Z register
            asm volatile ("eor r30,r30");
            asm volatile ("ijmp");          // jump to (Z)
            /
            soft_reset();
        }
        */
        set_sleep_mode(SLEEP_MODE_PWR_DOWN);
        //power_all_disable(); // turn power off to ADC, TIMER 1 and 2, Serial Interface
        //power_adc_disable();
        //-------------
        //sleep_mode(); //makes a call to three routines:  sleep_enable(); sleep_cpu(); sleep_disable();
        //-------------
        sleep_enable(); //sets the Sleep Enable bit in the MCUCR register
        sleep_cpu(); //issues the SLEEP command
        sleep_disable(); //clears the SE bit
        //-------------
        //power_all_enable(); // put everything on again
        //power_adc_enable();

        if (sleepLoop > deepSleep)
        {
            if(emptyBottle >= 3) { //Low Water LED

                blink(9,254);

                //Retry every 2 hours ...when someone refilled the bottle but did not cycle power.
                /*
                if((emptyBottle > 10 && sleepLoop > delayBetweenRefillReset) || (emptyBottle < 10 && sleepLoop > delayBetweenOverfloodReset)) {
                    soft_reset();
                }
                */
                if(ee != 0xFF || (emptyBottle > 10 && sleepLoop > delayBetweenRefillReset) || (emptyBottle < 10 && sleepLoop > delayBetweenOverfloodReset)) {
                    emptyBottle = 0;
                    moistureLog = 0;
                }
            }else{
                sleepLoop = 0;
                //======================
                //Prevents false-positive (empty detection)
                //Moisture sensor (too accurate) triggers exactly same value when dry
                //======================
                /*
                if (runSolar == 1 && sleepLogReset > delayBetweenLogReset) {
                    soft_reset();
                }else{
                    sleepLogReset++;
                }
                */
                //======================
                //Get Sensor Moisture
                //======================
                uint16_t moisture = sensorRead(sensorPin,moistureSensorPin);

                #ifdef EEPROM_ENABLED
                    EEPROM_save(0x1A,moisture,ee);
                #endif
                if(ee == 0xEA) { //LED Monitor enabled
                    /*
                    int number = 1234;
                    (number) % 10 => 4
                    (number / 10) % 10 => 3
                    (number / 100) % 10 => 2
                    (number / 1000) % 10 => 1
                    */
                    //=======================
                    //DEBUG (LED MORSE CODE)
                    //=======================
                    //for (uint16_t i = 1000 ; i >= 1; i=div10(i)) {
                    for (uint8_t i = 100 ; i >= 1; i /= 10) {
                        uint8_t d = (moisture/i) % 10;
                        d = d + d; //on + off timers (double loop)
                        blink(4,d); //blink a zero with a quick pulse
                        _delay_ms(1200);
                    }
                    //=======================
                }else if(ee == 0xEB || deepSleep > 255) { //Test Pump or Timer Trigger
                	emptyBottle = 0; //for timer trigger, disables flood prevention (otherwise 3 day will be 9 day sleep)
                    ee = 0xFF; //for test, run once
                	moisture = 8; //set low number
                	//EEPROM_save(0xA,ee,0xEE);
                }else {
                    //avoid this during the science project (data gathering)
                    /*
                	if(ee == 0xFF && (moisture - suitableMoisture) > 100) { //soil is too wet for set threshold, wait longer before checking again
                		deepSleep = 250; //8 seconds x 250 = 30 min
                	}else{
                        deepSleep = delayWatering; //Reset to regular monitoring
                    }
                    */
                    blink(3,2);
                }

                if(moisture < 4) { //Sensor Not in Soil

                    #ifdef UART_TX_ENABLED
                        uart_putu(suitableMoisture);
                        //uart_putc('\r');
                        //uart_putc('\n');
                    #endif

                    //_delay_ms(3000);
                    blink(1,18);
                
                #ifdef EEPROM_ENABLED
                }else if(moisture >= 1021) { //Sensor Manual Calibrate (cross/short both sensor leads)

                    #ifdef UART_TX_ENABLED
                        #ifdef ledPin
                            PORTB |= (1<<ledPin); //ON
                        #endif

                        for(uint8_t i = 0; i < 8; i++) //Get ready to place into base-line soil
                        {
                            uart_putc('.');
                            _delay_ms(800);
                        }
                        
                        #ifdef ledPin
                            PORTB &= ~(1<<ledPin); //OFF
                        #endif
                    #else
                        blink(9,9);
                    #endif

                    suitableMoisture = sensorRead(sensorPin,moistureSensorPin);

                    EEPROM_save(0x02,suitableMoisture,0xEE);
                #endif
                }else if (moisture < suitableMoisture) { //Water Plant

                    //===================
                    #ifdef SENSORLESS_ENABLED
                        //Detect Empty Bottle (Sensor-less)

                        //uint8_t m = moisture / 10;
                        moistureLog = moistureLog + moisture;

                        uint16_t mm = div3(moistureLog); //Average 3
                        //uint16_t mm = (moistureLog >> 2); //Average 4

                        if (mm > (moisture - 10) && mm < (moisture + 10)) {
                            emptyBottle = 11; //Pump ran but no change in moisture
                            //continue; //force next wait loop
                        }

                        errorCode = mm;
                    #endif

                    //===================
                    //Detect Empty Bottle (Sensored)
                    //===================
                    /*
                    loopback wire from water jug to Pin3 (PB4)
                    given power from Pin5 (PB0) while turning on NPN transistor
                    more accurate than sensor-less detection
                    */
                    /*
                    moisture = sensorRead(pumpPin,moistureSensorPin);

                    #ifdef EEPROM_ENABLED
                        EEPROM_save(0x1C,moisture,ee);
                    #endif

                    if (moisture > 10 && moisture < 255) { //avoid 0 detection if wire not connected
                        emptyBottle = 12;

                        #ifdef UART_TX_ENABLED
                            uart_putc('E');
                        #endif
                    }
                    */
                    if(emptyBottle < 3) { //Prevent flooding

                        #ifdef UART_TX_ENABLED
                            uart_putc('P');
                        #endif

                        if(ee != 0xEE) { //prevent actual water pumping during web-console
                            PORTB |= (1<<pumpPin); //ON
                        }
                        blink(potSize,2);
                        //PORTB &= ~(1<<pumpPin); //OFF

                        emptyBottle++; //Sensorless Empty Detection
                    }
                }else{
                    emptyBottle = 0;
                    moistureLog = 0;
                    errorCode = 0;
                }
            }
            #ifdef EEPROM_ENABLED
                EEPROM_save(0x38,emptyBottle,ee);
                EEPROM_save(0x3A,moistureLog,ee);
                EEPROM_save(0x2A,errorCode,ee);
            #endif
        }

        #ifdef SOLAR_ENABLED
            uint8_t voltage = 0;
            
            if(runSolar == 1) {
                /*
                (Optional TPL5110 = extreme efficiency 50nA! (nano-amp) sleep. Bypasses ATtiny ligic. Solar pin = DONE pin = Turnoff ATtiny)
                Note: Install both TPL5110 & LM2731
                */
                #ifdef TPL5110
                    DDRB |= (1<<solarPin); //Digital
                    PORTB |= (1<<solarPin); //High (5V)
                #endif
                /*
                (Optional TPL5110: If we are not off at this point TPL5110 was not installed,
                Do solar with ATtiny (Highly NOT recommened ...TPL5110 is the way to go)
                */

                DDRB &= ~(1<<solarSensorPin); //Shared pin with Sensor, Set Analog INPUT
                voltage = ReadADC(solarSensorPin, 1); //Detect Solar intensity - 300R inline + 10k pullup
                //DDRB |= (1<<solarSensorPin); //Shared pin with Sensor, set Digital OUTPUT
                
                #ifdef UART_TX_ENABLED
                    uart_putc(',');
                    uart_putu(voltage);
                #endif
                
                /*
                Regulators

                WS78L05 (TO92) linear "low efficiency" - turn on with GND
                LM2731 (SOT23) switching "high efficiency" - turn off with 5V
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

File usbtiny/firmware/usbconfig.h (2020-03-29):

/* Name: usbconfig.h
 * Project: V-USB, virtual USB port for Atmel's(r) AVR(r) microcontrollers
 * Author: Christian Starkjohann
 * Creation Date: 2005-04-01
 * Tabsize: 4
 * Copyright: (c) 2005 by OBJECTIVE DEVELOPMENT Software GmbH
 * License: GNU GPL v2 (see License.txt), GNU GPL v3 or proprietary (CommercialLicense.txt)
 */

#ifndef __usbconfig_h_included__
#define __usbconfig_h_included__

/*
General Description:
This file is an example configuration (with inline documentation) for the USB
driver. It configures V-USB for USB D+ connected to Port D bit 2 (which is
also hardware interrupt 0 on many devices) and USB D- to Port D bit 4. You may
wire the lines to any other port, as long as D+ is also wired to INT0 (or any
other hardware interrupt, as long as it is the highest level interrupt, see
section at the end of this file).
+ To create your own usbconfig.h file, copy this file to your project's
+ firmware source directory) and rename it to "usbconfig.h".
+ Then edit it accordingly.
*/

/* ---------------------------- Hardware Config ---------------------------- */

/*	#define USB_CFG_IOPORTNAME      D	*/
/* This is the port where the USB bus is connected. When you configure it to
 * "B", the registers PORTB, PINB and DDRB will be used.
 */
/*	#define USB_CFG_DMINUS_BIT      4	*/
/* This is the bit number in USB_CFG_IOPORT where the USB D- line is connected.
 * This may be any bit in the port.
 */
/*	#define USB_CFG_DPLUS_BIT       2	*/
/* This is the bit number in USB_CFG_IOPORT where the USB D+ line is connected.
 * This may be any bit in the port. Please note that D+ must also be connected
 * to interrupt pin INT0! [You can also use other interrupts, see section
 * "Optional MCU Description" below, or you can connect D- to the interrupt, as
 * it is required if you use the USB_COUNT_SOF feature. If you use D- for the
 * interrupt, the USB interrupt will also be triggered at Start-Of-Frame
 * markers every millisecond.]
 */
#if defined (__AVR_ATtiny45__) || defined (__AVR_ATtiny85__)
#define USB_CFG_IOPORTNAME      B
#define USB_CFG_DMINUS_BIT      4
#define USB_CFG_DPLUS_BIT       3

#elif __AVR_ATtiny10__
#define USB_CFG_IOPORTNAME      B
#define USB_CFG_DMINUS_BIT      0
#define USB_CFG_DPLUS_BIT       1

#endif

#define USB_CFG_CLOCK_KHZ       (F_CPU/1000)
/* Clock rate of the AVR in kHz. Legal values are 12000, 12800, 15000, 16000,
 * 16500, 18000 and 20000. The 12.8 MHz and 16.5 MHz versions of the code
 * require no crystal, they tolerate +/- 1% deviation from the nominal
 * frequency. All other rates require a precision of 2000 ppm and thus a
 * crystal!
 * Since F_CPU should be defined to your actual clock rate anyway, you should
 * not need to modify this setting.
 */
#if USB_CFG_CLOCK_KHZ==18000
#define USB_CFG_CHECK_CRC       1
#else
#define USB_CFG_CHECK_CRC       0
#endif
/* Define this to 1 if you want that the driver checks integrity of incoming
 * data packets (CRC checks). CRC checks cost quite a bit of code size and are
 * currently only available for 18 MHz crystal clock. You must choose
 * USB_CFG_CLOCK_KHZ = 18000 if you enable this option.
 */

/* ----------------------- Optional Hardware Config ------------------------ */

/* #define USB_CFG_PULLUP_IOPORTNAME   D */
/* If you connect the 1.5k pullup resistor from D- to a port pin instead of
 * V+, you can connect and disconnect the device from firmware by calling
 * the macros usbDeviceConnect() and usbDeviceDisconnect() (see usbdrv.h).
 * This constant defines the port on which the pullup resistor is connected.
 */
/* #define USB_CFG_PULLUP_BIT          4 */
/* This constant defines the bit number in USB_CFG_PULLUP_IOPORT (defined
 * above) where the 1.5k pullup resistor is connected. See description
 * above for details.
 */

/* --------------------------- Functional Range ---------------------------- */
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

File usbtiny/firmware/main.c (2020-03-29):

/* Name: main.c
  
  created by chris chung, 2010 April

  based on the works found in

  v-usb framework http://www.obdev.at/vusb/
	 Project: Thermostat based on AVR USB driver
	 Author: Christian Starkjohann
    
  usbtiny isp http://www.xs4all.nl/~dicks/avr/usbtiny/
  	Dick Streefland
  
  please observe licensing term from the above two projects

	Copyright (C) 2010  chris chung

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

  **** fuse setting, 
  **** this will blow reset fuse, u will need to use HV programmer to recover if u mess up
  avrdude -c usbtiny -p t45 -V -U lfuse:w:0xe1:m -U hfuse:w:0x5d:m -U efuse:w:0xff:m 
 */

#include <avr/io.h>
#include <avr/wdt.h>
#include <avr/eeprom.h>
#include <avr/interrupt.h>
#include <avr/pgmspace.h>
#include <util/delay.h>
#include <stdlib.h>

#include "usbdrv.h"
//#include "oddebug.h"

enum
{
	// Generic requests
	USBTINY_ECHO = 0,		// echo test
	USBTINY_READ = 1,		// read byte
	USBTINY_WRITE = 2,		// write byte
	USBTINY_CLR = 3,		// clear bit 
	USBTINY_SET = 4,		// set bit
	// Programming requests
	USBTINY_POWERUP = 5,	// apply power (wValue:SCK-period, wIndex:RESET)
	USBTINY_POWERDOWN = 6,	// remove power from chip
	USBTINY_SPI = 7,		// issue SPI command (wValue:c1c0, wIndex:c3c2)
	USBTINY_POLL_BYTES = 8,	// set poll bytes for write (wValue:p1p2)
	USBTINY_FLASH_READ = 9,	// read flash (wIndex:address)
	USBTINY_FLASH_WRITE = 10,	// write flash (wIndex:address, wValue:timeout)
	USBTINY_EEPROM_READ = 11,	// read eeprom (wIndex:address)
	USBTINY_EEPROM_WRITE = 12,	// write eeprom (wIndex:address, wValue:timeout)
	USBTINY_DDRWRITE = 13,	// set port direction
	//USBTINY_SPI1 = 14		// a single SPI command
};

#define	PORT	PORTB
#define	DDR		DDRB
#define	PIN		PINB

//
// to reduce pin count so that this can fit in a 8 pin tiny
// . no power nor ground pins to target, they are to be connected always
// . no reset control pin to target, target reset always grounded
//   * this had caused problem and there are two solutions
//     1. provide a toggle switch to off-on-off target reset to ground
//     2. introduce reset control and use reset pin as io
//
#define	POWER_MASK	0x00
#define	GND_MASK	0x00

#define	RESET_MASK	(1 << 5)
#define	SCK_MASK	(1 << 2)
#define	MISO_MASK	(1 << 1)
#define	MOSI_MASK	(1 << 0)

// ----------------------------------------------------------------------
// Programmer input pins:
//	MISO	PD3	(ACK)
// ----------------------------------------------------------------------

// ----------------------------------------------------------------------
// Local data
// ----------------------------------------------------------------------
static	uchar		sck_period = 10;	// SCK period in microseconds (1..250)
static	uchar		poll1;		// first poll byte for write
static	uchar		poll2;		// second poll byte for write
static	unsigned		address;	// read/write address
static	unsigned		timeout;	// write timeout in usec
static	uchar		cmd0;		// current read/write command byte
static	uchar		cmd[4];		// SPI command buffer
static	uchar		res[4];		// SPI result buffer

// ----------------------------------------------------------------------
// Delay exactly <sck_period> times 0.5 microseconds (6 cycles).
// ----------------------------------------------------------------------
__attribute__((always_inline))
static inline void delay ( void )
{
	asm volatile(
		"	mov	__tmp_reg__,%0	\n"
		"0:	rjmp	1f		\n"
		"1:	nop			\n"
		"	dec	__tmp_reg__	\n"
		"	brne	0b		\n"
		: : "r" (sck_period) );
}

// ----------------------------------------------------------------------
// Issue one SPI command.
// ----------------------------------------------------------------------
static	void	spi ( uchar* cmd, uchar* res, uchar n )
{
	uchar	c;
	uchar	r;
	uchar	mask;

	while	( n != 0 )
	{
		n--;
		c = *cmd++;
		r = 0;
		for	( mask = 0x80; mask; mask >>= 1 )
		{
			if	( c & mask )
			{
				PORT |= MOSI_MASK;
			}
			delay();
			PORT |= SCK_MASK;
			delay();
			r <<= 1;
			if	( PIN & MISO_MASK )
			{
				r++;
			}
			PORT &= ~MOSI_MASK;
			PORT &= ~SCK_MASK;
		}
		*res++ = r;
	}
}

// ----------------------------------------------------------------------
// Create and issue a read or write SPI command.
// ----------------------------------------------------------------------
static	void	spi_rw ( void )
{
	unsigned	a;

	a = address++;
	if	( cmd0 & 0x80 )
	{	// eeprom
		a <<= 1;
	}
	cmd[0] = cmd0;
	if	( a & 1 )
	{
		cmd[0] |= 0x08;
	}
	cmd[1] = a >> 9;
	cmd[2] = a >> 1;
	spi( cmd, res, 4 );
}

// ----------------------------------------------------------------------
// Handle an IN packet.
// ----------------------------------------------------------------------
uchar usbFunctionRead(uchar *data, uchar len)
{
	uchar	i;

	for	( i = 0; i < len; i++ )
	{
		spi_rw();
		data[i] = res[3];
	}
	return len;
}

// ----------------------------------------------------------------------
// Handle an OUT packet.
// ----------------------------------------------------------------------
uchar usbFunctionWrite(uchar *data, uchar len)
{
	uchar	i;
	unsigned	usec;
	uchar	r;
	//uchar	last = (len != 8);

	for	( i = 0; i < len; i++ )
	{
		cmd[3] = data[i];
		spi_rw();
		cmd[0] ^= 0x60;	// turn write into read
		//
		for	( usec = 0; usec < timeout; usec += 32 * sck_period )
		{	// when timeout > 0, poll until byte is written
			spi( cmd, res, 4 );
			r = res[3];
			if	( r == cmd[3] && r != poll1 && r != poll2 )
			{
				break;
			}
		}
		//
	}
	//return last;
	return 1;
}

/* ------------------------------------------------------------------------- */
/* ------------------------ interface to USB driver ------------------------ */
/* ------------------------------------------------------------------------- */
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

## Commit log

2018-05-20 schematics update
    [main.fzz]
2019-01-13 added pcb design
    [main.brd, main.sch]
2019-01-14 pcb adjustments
    [main.brd, main.sch]
2019-01-14 a few more corrections
    [main.brd, main.sch]
2019-01-15 optimized pcb and code
    [main.brd, main.sch]
2019-01-16 Rev 0.3
    [main.brd, main.fzz, main.sch]
2019-01-18 Rev 0.4
    [main.brd, main.sch]
2019-02-09 Rev 0.5
    [main.brd, main.sch]
2019-03-05 added version track
2019-07-09 code updates
    [main.brd, main.sch]
2019-07-13 rev 0.6
    [main.brd, main.sch]
2019-07-14 added switching regulator
    [main.brd, main.sch]
2019-07-15 calibrated solar
    [main.brd, main.sch]
2019-07-17 solar parameters tuned
    [main.brd, main.sch]
2019-08-15 calibrated battery
2019-12-24 new graphics
    [main.brd, main.sch]
2019-12-27 removed bootloader added USBasp
    [main.brd, main.sch]
2019-12-29 windows drivers
2020-01-01 improved solar
    [main.brd, main.sch, usbasp.brd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]
2020-01-03 remapped LED gpio
    [main.brd, main.sch]
2020-02-05 many updates
    [main.brd, main.sch, usbasp.brd]
2020-02-12 added usbtiny + many updates
    [usbasp.brd, usbasp.sch, vusbtiny.brd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]
2020-02-15 rev 0.8 (usbtiny built-in)
    [main.brd, main.sch]
2020-03-24 improved clock calibration
2020-03-28 lots of updates
    [main.brd, usbasp.brd, usbasp.sch]
2020-03-29 rev 0.9
    [main.brd, main.sch]
2020-04-02 changed ADC ref to 1.1V
2020-04-07 fixed linux and added graph
    [main.c]
2020-04-13 added usb diode
    [main.brd, main.sch]
2020-04-13 low battery detection
    [main.brd]
2020-04-16 adc noise reduction code
    [main.c, uart.c]
2020-04-22 reset pin filter capacitor
    [main.brd, main.sch]
2020-04-24 major bug fix - force pump turn off
    [main.c]
2020-05-03 firmware updates
    [main.brd, main.sch]
2020-05-29 added manual timer feature
2020-06-01 timer code fix
2020-06-06 eeprom uint16 value fix
    [main.c]

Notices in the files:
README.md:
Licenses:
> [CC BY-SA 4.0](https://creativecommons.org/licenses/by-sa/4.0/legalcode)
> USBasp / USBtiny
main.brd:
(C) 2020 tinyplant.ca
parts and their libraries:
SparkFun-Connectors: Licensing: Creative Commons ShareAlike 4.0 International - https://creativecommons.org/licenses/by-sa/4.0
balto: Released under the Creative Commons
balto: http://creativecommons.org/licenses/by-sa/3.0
